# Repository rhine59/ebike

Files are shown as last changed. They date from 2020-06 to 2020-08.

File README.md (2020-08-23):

# Fitting a TongSheng TSDZ2 mid drive motor with an 8 pin controller to a 52v battery and the Bafang 860C LCD

<!-- TOC -->

- [Fitting a TongSheng TSDZ2 mid drive motor with an 8 pin controller to a 52v battery and the Bafang 860C LCD](#fitting-a-tongsheng-tsdz2-mid-drive-motor-with-an-8-pin-controller-to-a-52v-battery-and-the-bafang-860c-lcd)
- [Building a `bootloader` to flash the 860c display](#building-a-bootloader-to-flash-the-860c-display)
  - [Skills](#skills)
  - [Tips](#tips)
  - [Tools that I used.](#tools-that-i-used)
  - [Sourcing components and building the bootloader.](#sourcing-components-and-building-the-bootloader)
  - [Adjusting the output voltage from the DC Booster](#adjusting-the-output-voltage-from-the-dc-booster)
- [Flashing the firmware of the TSDZ2 motor controller](#flashing-the-firmware-of-the-tsdz2-motor-controller)
  - [ST-Link V2 pinouts](#st-link-v2-pinouts)
- [Connecting the 860C display to the 8pin TSDZ2 harness.](#connecting-the-860c-display-to-the-8pin-tsdz2-harness)
- [Other collected information](#other-collected-information)

<!-- /TOC -->

There is not much original content here, I am walking in the footsteps of those who know more than me, but hope that pulling all the threads together that I needed is of help to those who follow. I hope that I have given all the credits and references that are due, but if I have missed anything, then please contact me and I will happily update this content.

I am in no way trying to place product here. Any images or links are provided as samples that illustrate the story and as they worked for me. There are likely to be other ways to achieve the same result, but this journal is here to chronicle my journey.

Any prices quoted here are only indicative and there will be options at different prices. Listed here to help you understand outline costs.

# Building a `bootloader` to flash the 860c display

See the following for the original reference materials.

[TSDZ2 Wiki](https://github.com/OpenSource-EBike-firmware/TSDZ2_wiki/wiki/Flash-the-firmware-on-860C-850C-using-bootloader)

[Eco Cycles](https://www.eco-ebike.com/blogs/eco-cycles-instructionals/850c-tsdz2-open-source-firmware-bootloader-update-tutorial)

## Skills

I am not an expert in this topic, but if you can do some basic soldering, have some basic PC skills and can follow a recipe, then this should be well within your grasp. This is 90% planning and 10% execution.

## Tips

1. Read and understand, don't learn and make mistakes as you go.
2. Think, think some more, think again and then cut.

## Tools that I used.

<p float="left">
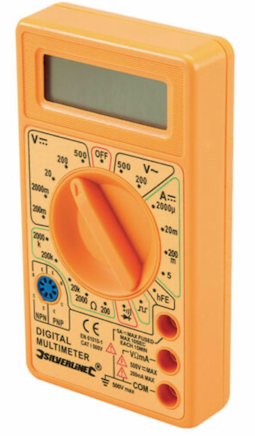
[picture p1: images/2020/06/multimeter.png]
  
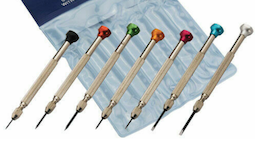
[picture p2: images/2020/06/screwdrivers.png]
  
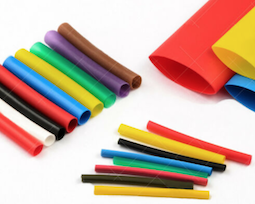
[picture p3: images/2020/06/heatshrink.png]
  
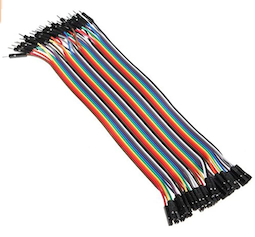
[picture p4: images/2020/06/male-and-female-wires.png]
  
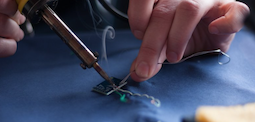
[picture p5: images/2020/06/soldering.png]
  
</p>

- Multimeter - 0 volts to 40 volts DC.
- Watch makers screwdrivers to adjust output voltage of XL6009 DC Step Up converter.
- Heatshrink tubing to provide electrical isolation and assembly strength. `£2`
- Dupont wires for connecting components. You will need the female ended connectors, suggest you buy female/female wires as you will need them to flash the TSDZ2. `£2`
- Solder / Flux / Iron - I assume that you have access to these already.

## Sourcing components and building the bootloader.

I have used the schematic from [here](https://github.com/OpenSource-EBike-firmware/TSDZ2_wiki/wiki/Flash-the-firmware-on-860C-850C-using-bootloader)

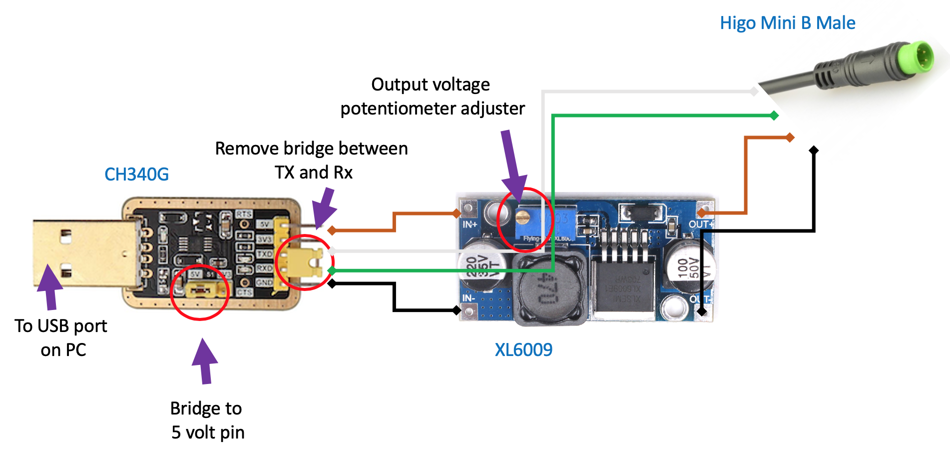
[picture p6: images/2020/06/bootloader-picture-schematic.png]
bootloader picture schematic


From    | Pin | Colour | Pin | Via    | Pin  | Colour | To
--------|-----|--------|-----|--------|------|--------|-------
CHG340G | 5V  | Brown  | IN+ | XL6009 | OUT+ | Brown  | HIGO B
CHG340G | GND | Black  | IN- | XL6009 | OUT- | Black  | HIGO B
CHG340G | TXD | White  | --> | ---->  | -->  | White  | HIGO B
CHG340G | RXD | Green  | --> | ---->  | -->  | Green  | HIGO B

Following the recipe [here](https://github.com/OpenSource-EBike-firmware/TSDZ2_wiki/wiki/Flash-the-firmware-on-860C-850C-using-bootloader), I sourced the following parts.

1. `A CH340G RS232 to USB TTL Auto Converter Adapter` to take the signal from the `APT Burn Tools` updating software and deliver it to the `860c` LCD display. `£3.20`

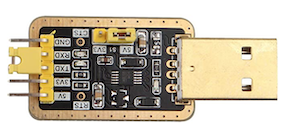
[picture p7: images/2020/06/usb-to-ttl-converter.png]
USB to TTL converter


[EBAY Search](https://www.ebay.co.uk/sch/i.html?_from=R40&_trksid=m570.l1313&_nkw=CH340+Gold+USB+TTL&_sacat=0)

2. `A 5 pin Higo Mini B extension cable - male to male`. You will cut this in half, use 1 half to create the bootloader, and the other will attach to the end of the 860c LCD connection to the motor controller. `£10`

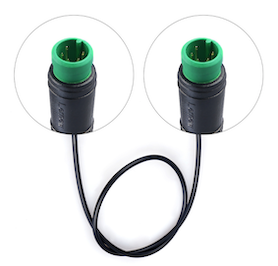
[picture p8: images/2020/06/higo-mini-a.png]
Higo Mini A


[Amazon search](https://www.amazon.co.uk/Bafang-Extended-Cable-Display-750C/dp/B07GDL1TSN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)

3. `An XL6009 DC-DC Voltage Step Up Boost Converter` to take a 5V supply from your laptop and then boost it to the 30v required to drive the 860C LCD while it is being updated. `£3`

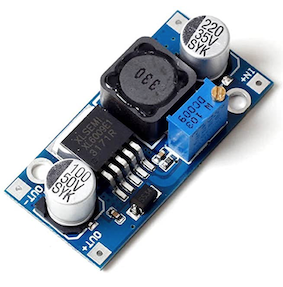
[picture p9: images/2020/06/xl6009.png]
xl6009


[Ebay search](https://www.ebay.co.uk/sch/i.html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)

When assembled, the `bootloader` looked liked this for me and would have cost about `£20` if I had had to buy all the bits. There are other components that you can use and I am sure that it could be completed the build for less money.

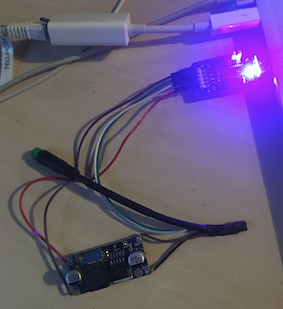
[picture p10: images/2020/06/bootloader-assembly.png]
bootloader assembly


Now that we have built the `bootloader`, we need to adjust the voltage supply that will reach the 860c display LCD as we have a 5 volt supply coming from the USB port on your PC but we need a 30 volt supply to the 860c.

## Adjusting the output voltage from the DC Booster

Check that the jumpers on your `CH340G` are set to provide `5 volts` and not `3.3 volts` as below.

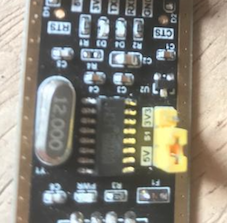
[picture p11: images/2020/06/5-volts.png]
5 volts


You will see that the USB connection from your laptop will supply 5 volts to the `in+` `in-` side of the `XL6009 DC Step up boost converter`.

Check the voltage delivered to the `XL6009` ....

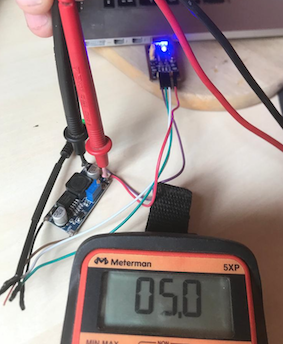
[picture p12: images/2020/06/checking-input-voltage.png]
checking input voltage


We now need to adjust the `XL6009` so that we are delivering the required voltage to the `860c` LCD display.

You need to adjust the potentiometer (little screw on the blue block) so that the output voltage from the buck converter is 30 volts. You will need to use your multimeter to measure the DC voltage on the `+out` and `-out` side of the `XL6009`.

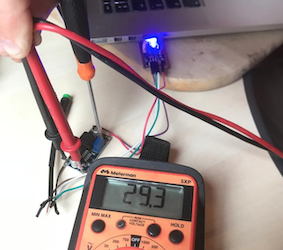
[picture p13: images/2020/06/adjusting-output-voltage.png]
adjusting output voltage


Now we have 30 volts output and are ready to flash the `860c` LCD display.

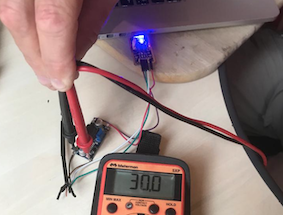
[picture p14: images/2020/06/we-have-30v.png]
we have 30v


# Flashing the firmware of the TSDZ2 motor controller

You will need

1. An `ST-Link V2` to provide the link from the software on your PC to the `throttle sensor` inputs to your TSDZ2 motor controller. Some `ST-Link V2` sellers provide 4 x Dupont connectors, but you will need a total of `7` connectors if you are building a `bootloader` to flash your 860C display and are flashing your TSDZ2 motor controller.

Remember that the software versions on the controller and display operate as a pair, so you are upgrading both if you are upgrading any.

`£3`

[Ebay Search](https://www.ebay.co.uk/sch/i.html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)

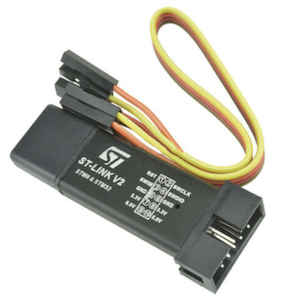
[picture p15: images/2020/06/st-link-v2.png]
st-link-v2


.....

`ST-Link V2` connected to the `throttle` connector from the TSDZ2 harness

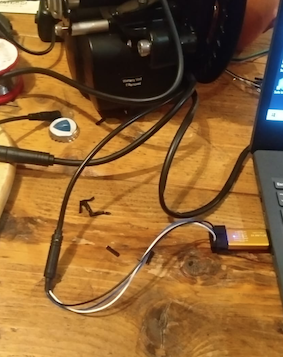
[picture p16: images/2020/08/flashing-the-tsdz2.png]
flashing the tsdz2


When complete, you will see `update complete` on the PC screen.

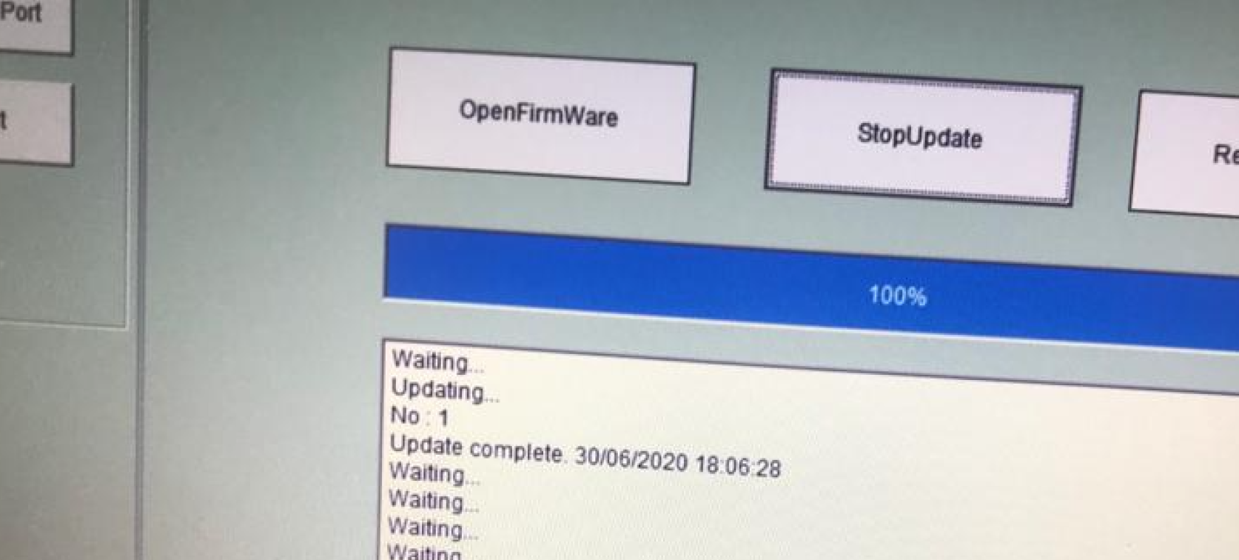
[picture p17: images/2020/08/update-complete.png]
update complete


2. `Dupont` wire connectors - female to female.

`£2`

[Ebay search](https://www.ebay.co.uk/sch/i.html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)

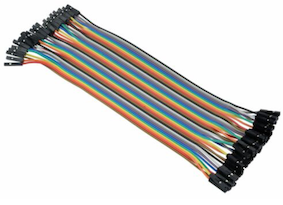
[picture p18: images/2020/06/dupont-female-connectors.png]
Dupont female connectors


## ST-Link V2 pinouts

I have found that the pin outs on the `ST-Link V2` vary, so have a look at the diagram on the face of the device and understand how your pinouts are organised.

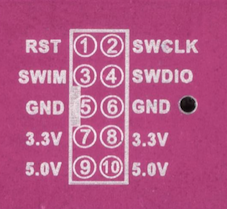
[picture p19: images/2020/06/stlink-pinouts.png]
stlink pinouts


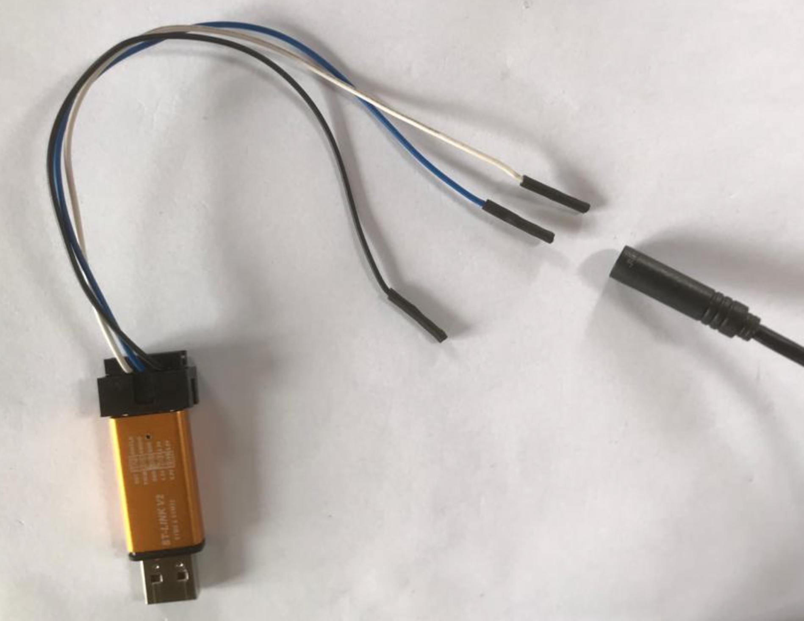
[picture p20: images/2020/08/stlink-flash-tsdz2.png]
stlink flash tsdz2


# Connecting the 860C display to the 8pin TSDZ2 harness.

Others have been here before me and special thanks to `Ben Garside` (bejam) on the [endless-sphere ](https://endless-sphere.com/forums/viewtopic.php?f=30&t=93818&p=1575340&hilit=bejam#p1575340) website for his support.

Before we start, here is an overview of what we are going to do.

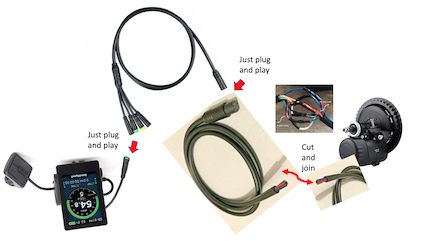
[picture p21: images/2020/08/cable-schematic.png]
cable schematic


To do this we will need ....

1. An `8pin female Higo cable`

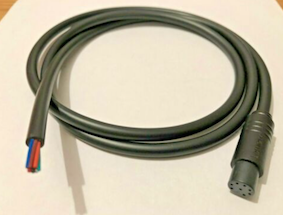
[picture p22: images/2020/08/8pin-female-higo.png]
8pin female Higo


I sourced mine on `Ebay` by searching on `Higo Waterproof Connector 2 3 4 5 6 8 pin cable lead 1m ebike electric bafang`

`£8.99` in my case.

Here is a picture of the TSDZ2 with associated cables.

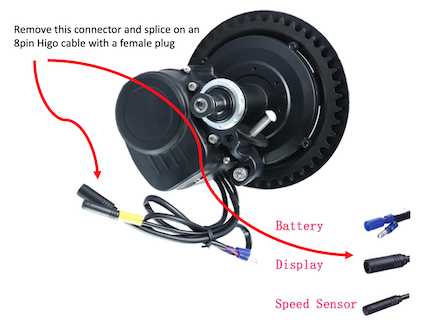
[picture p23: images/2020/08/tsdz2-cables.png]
tsdz2 cables


This needs connecting to the 8pin harness from the `TSDZ2` motor, so you will need remove the existing female Higo connector and then reconnect the wires from the 8pin harness cable to the 8pin Higo cable. The wires are the same colour, but they need to be connected as follows:-

8pin female Higo cable | 8pin 1T4 cable from TSDZ2 | Function
-----------------------|---------------------------|---------
blue                   | brown                     | P+
red                    | orange                    | PL
yellow                 | yellow                    | Rx
white                  | red                       | 5V
green                  | white                     | brake
orange                 | blue                      | throttle
brown                  | green                     | Tx
black                  | black                     | GND

`Helping Hands` are a great help for this job. Make sure that you insulate each solder joint with shrink wrap and then shrink wrap the completed bundle again to provide strength and protection from the elements.

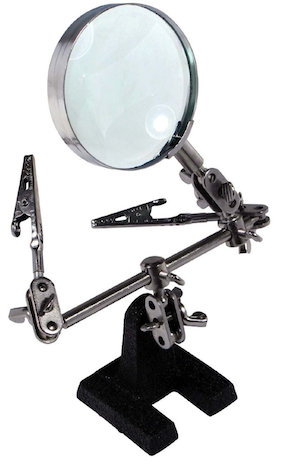
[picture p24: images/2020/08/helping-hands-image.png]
helping hands image


In use for this job ....

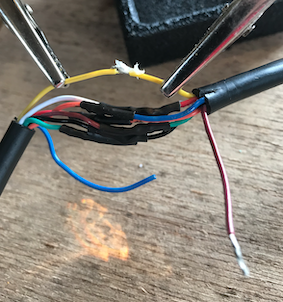
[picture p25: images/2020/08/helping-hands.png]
helping hands


When complete but before final weather proofing.

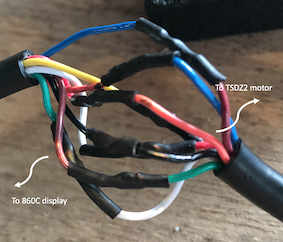
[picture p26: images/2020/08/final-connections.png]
final connections


2. You will need a harness that you connect to your new 8 pin female Higo connector on your `TSDZ2` motor harness that then splits to feed display, brakes (2) and throttle. The image below gives a good overview of the connectors in the harness and what they are used for.

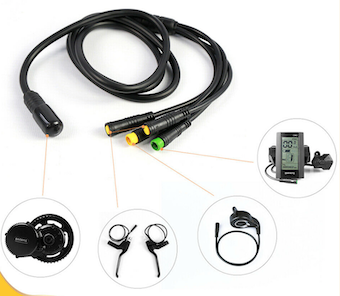
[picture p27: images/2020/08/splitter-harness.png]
splitter harness


I again sourced by cable on `Ebay` using a `Ebike Accessories Harness Higo 1T4 Wiring Cable for Bafang Mid Motor Kit BBS0102` search and paid `£13.99`.

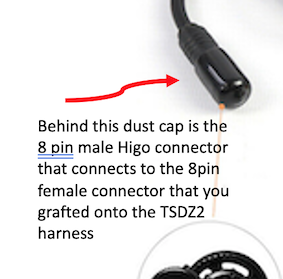
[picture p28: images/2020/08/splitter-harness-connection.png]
splitter harness connection


# Other collected information

[Bafang BBSHD Wiring Diagram](https://endless-sphere.com/forums/viewtopic.php?f=28&t=79788&start=5200)

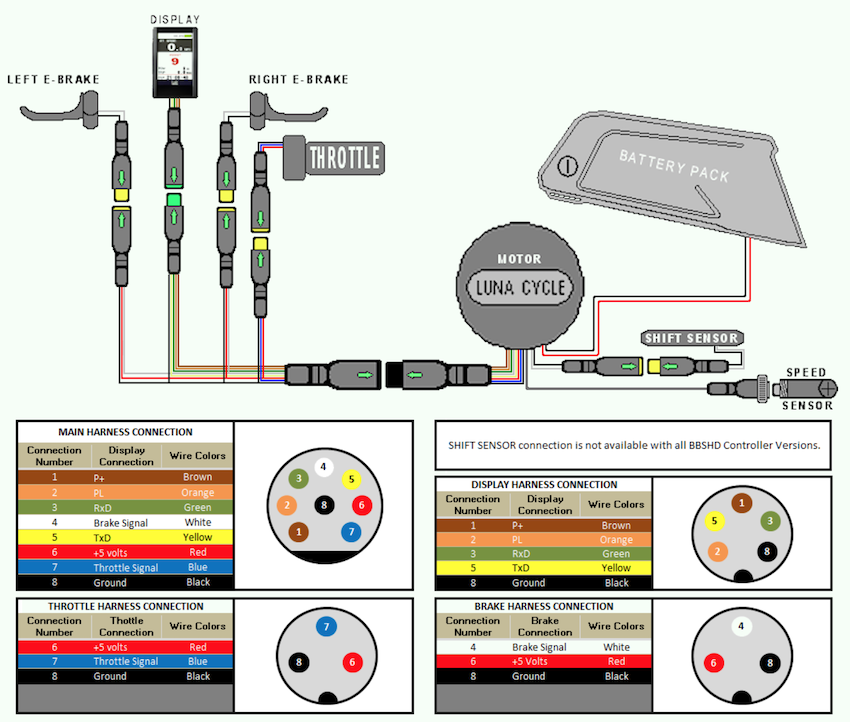
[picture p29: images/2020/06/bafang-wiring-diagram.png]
bafang wiring diagram


[Bottom bracket dimensions](https://greenpedel.en.made-in-china.com/product/UNSnMspdyyWh/China-Greenpedel-MID-Drive-Motor-Tsdz-2-36V-500W-Electric-Bicycle-Motor-Kit.html)

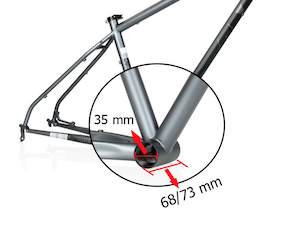
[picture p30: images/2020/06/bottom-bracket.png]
bottom bracket


[Ebay search](https://www.ebay.co.uk/sch/i.html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)

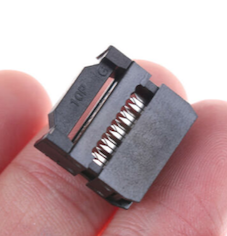
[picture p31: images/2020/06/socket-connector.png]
socket connector


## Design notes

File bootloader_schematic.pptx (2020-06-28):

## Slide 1

Higo Mini B Male

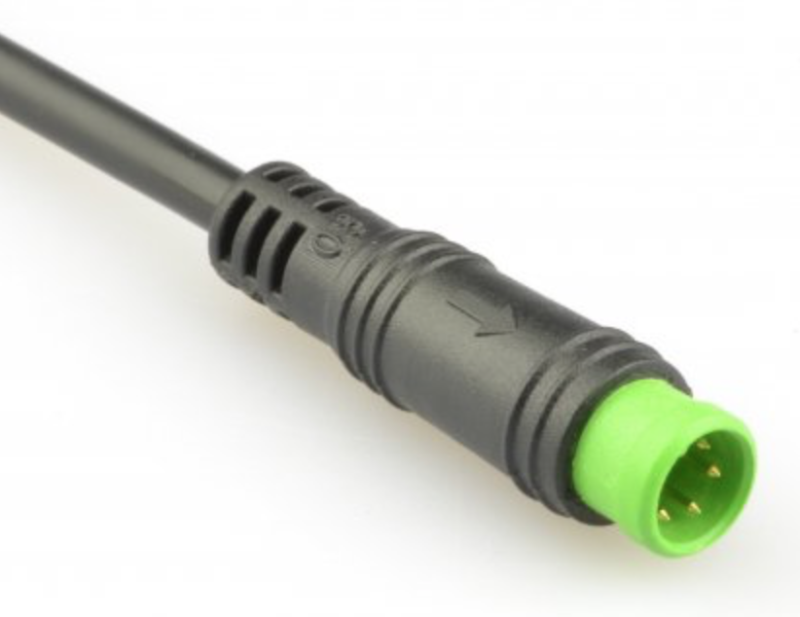
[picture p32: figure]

Output voltage
potentiometer adjuster

Remove bridge between
TX and Rx

CH340G

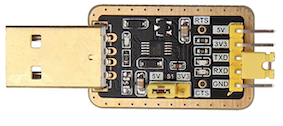
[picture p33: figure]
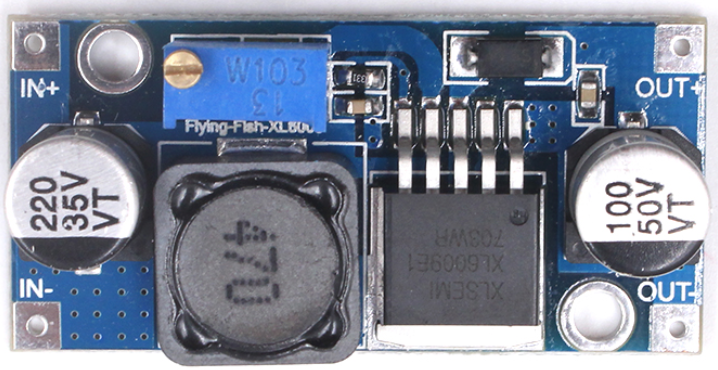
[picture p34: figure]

To USB port
on PC

XL6009

Bridge to
5 volt pin

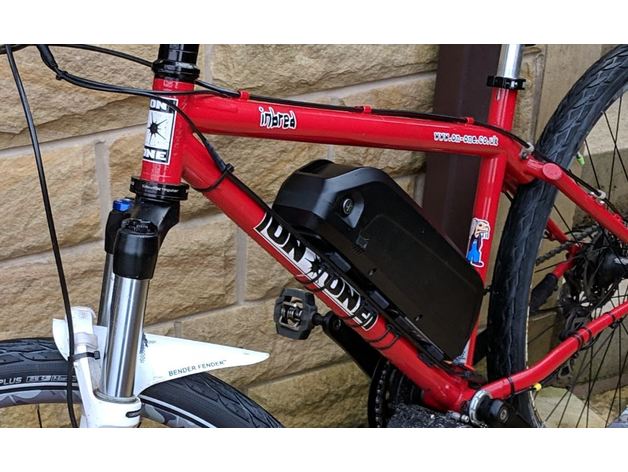
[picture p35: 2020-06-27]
Hailong_style_Ebike_Battery_Mounts/images/0f4a6f495f26ff8e57ab981901b127b3_preview_featured.jpg

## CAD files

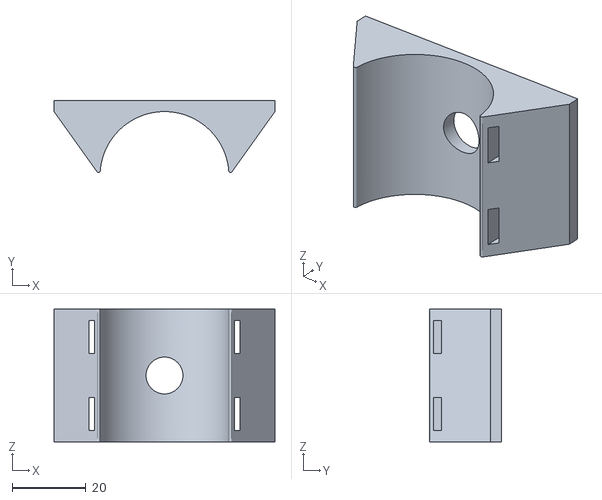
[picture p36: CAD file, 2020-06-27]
Hailong_style_Ebike_Battery_Mounts/files/bike_battery_mounts_with_twin_tie_wraps_bottle_mount_no_cable_mount.stl
60.0 x 19.5 x 36.0

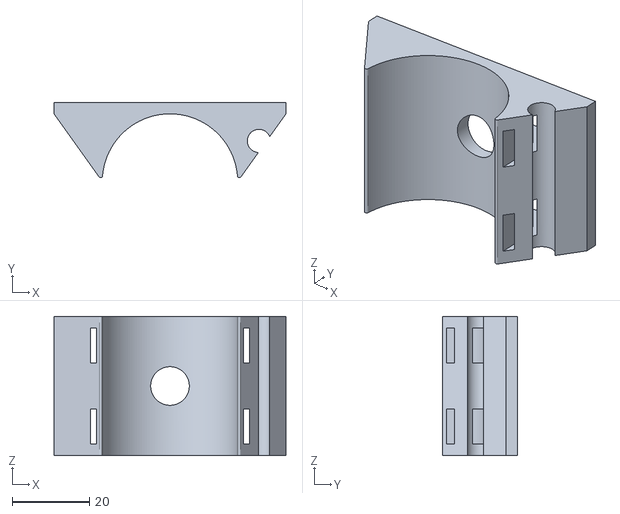
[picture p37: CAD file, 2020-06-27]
Hailong_style_Ebike_Battery_Mounts/files/bike_battery_mounts_with_twin_tie_wraps.stl
60.0 x 19.5 x 36.0

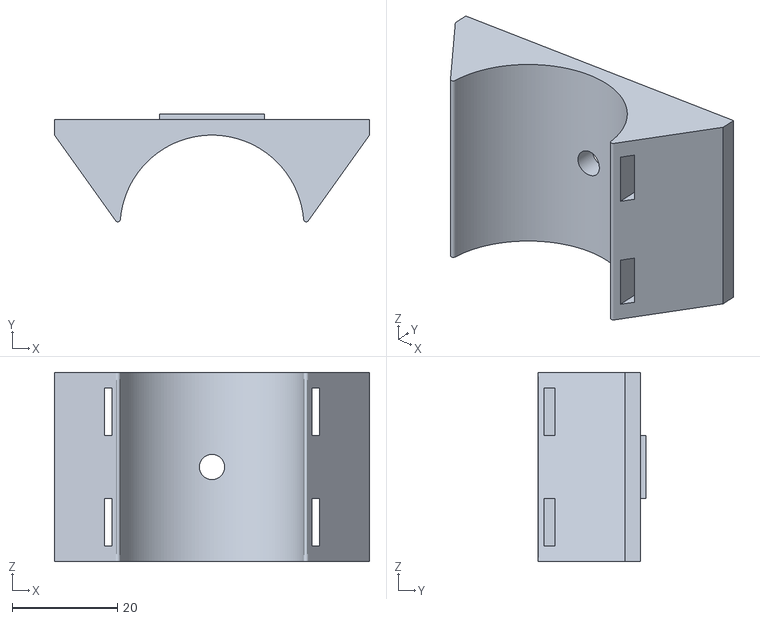
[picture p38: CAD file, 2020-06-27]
Hailong_style_Ebike_Battery_Mounts/files/bike_battery_mounts_with_twin_tie_wraps_screw_no_cable_mount.stl
60.0 x 20.5 x 36.0

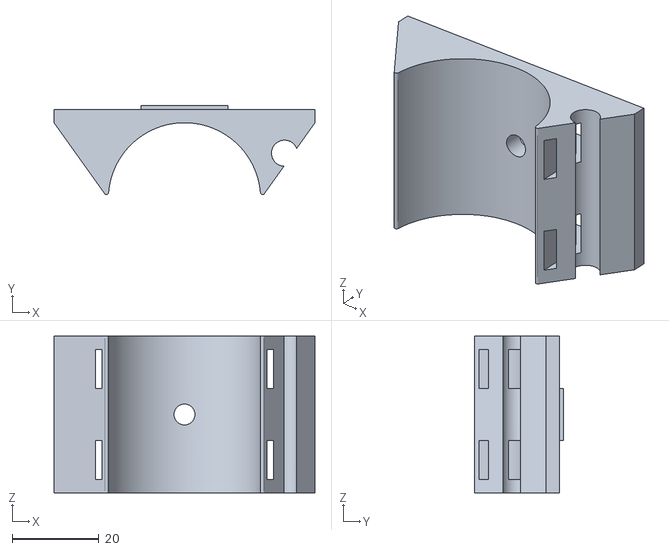
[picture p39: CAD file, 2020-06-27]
Hailong_style_Ebike_Battery_Mounts/files/bike_battery_mounts_with_twin_tie_wraps_screw.stl
60.0 x 20.5 x 36.0
